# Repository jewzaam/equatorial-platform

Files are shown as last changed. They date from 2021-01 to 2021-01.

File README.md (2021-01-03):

Welcome to my equatorial platform journey.  This is a work in progress, but I'm pretty obsessed with it lately so expect to get something built to test it out soon.

License: [CC BY-NC-SA-3.0](https://creativecommons.org/licenses/by-nc-sa/3.0/)

Documents are in the [docs](docs/) directory.

OpenSCAD source is in the [src](src/) directory.

Generated STL is in the [stl](stl/) directory.

# Docs Index

* [Introduction](docs/05-introduction.md)
* [Getting Started](docs/10-getting-started.md)
* [Model: Platform Top](docs/30-model-platform-top.md)
* [Model: Platform Bottom](docs/50-model-platform-bottom.md)
* [References](docs/99-references.md)

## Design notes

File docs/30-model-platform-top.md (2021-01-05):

# Model: Top Platform

## Basic Platform
For the purposes of this document the platform (brown) is represented as a triangle.  In practice it can be whatever shape you like so long as it’s heavy enough and your telescope fits on it.
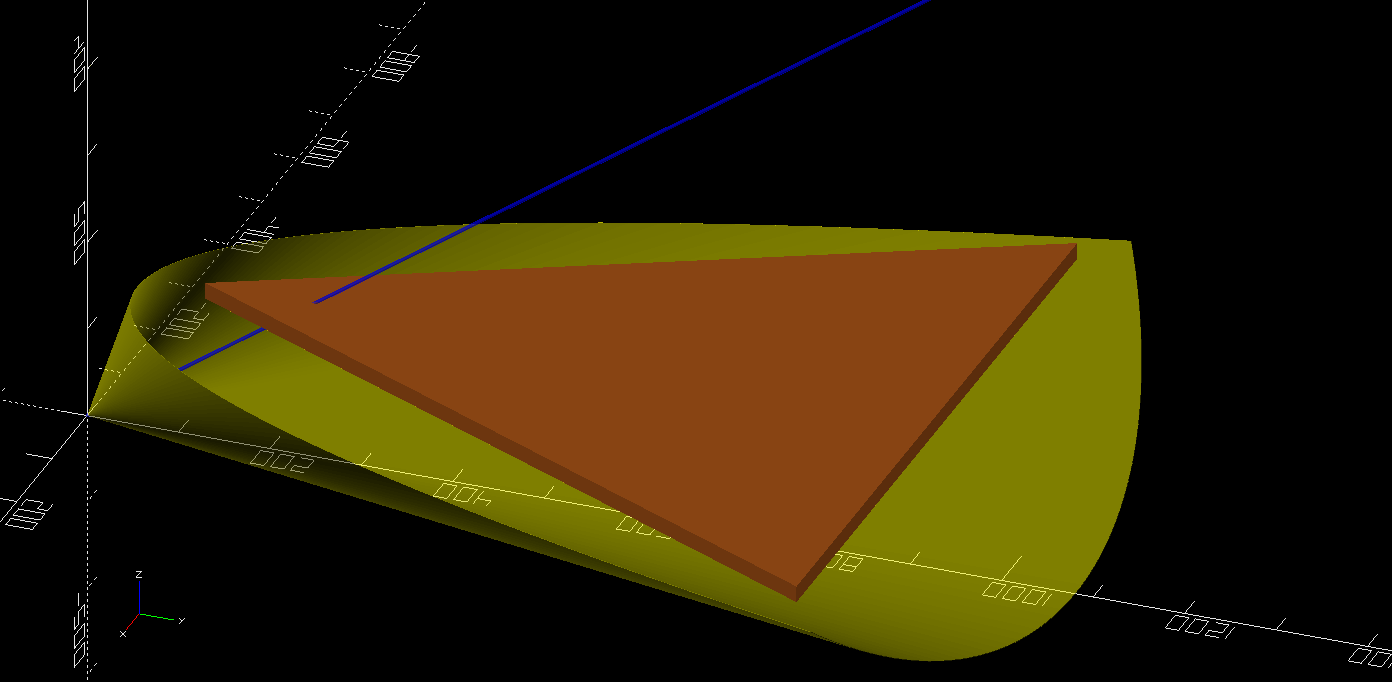
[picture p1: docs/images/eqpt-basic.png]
Basic Platform


## Our Cone
The foundation of an equatorial platform is spilling a cone (yellow) to compensate for earth’s rotation.  So we take the latitude where the platform is going to be used and start with a cone on its side with the center axis (blue) raised at the latitude.
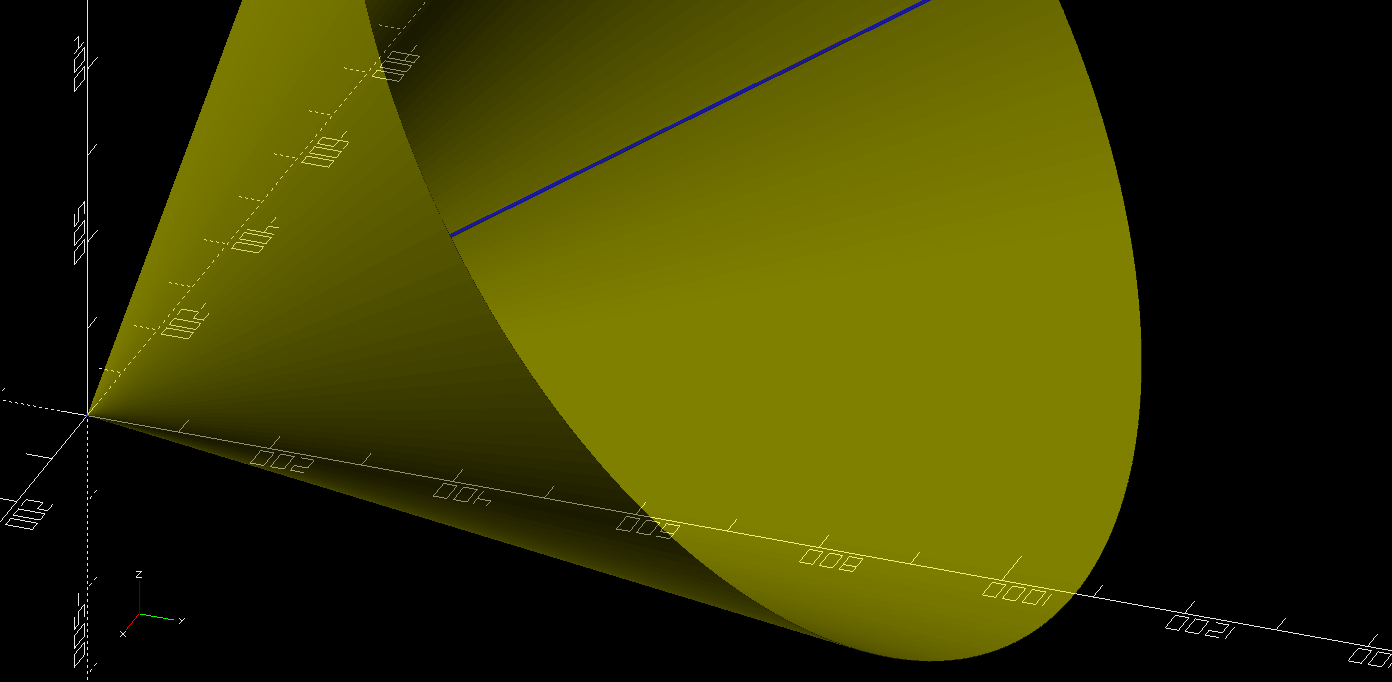
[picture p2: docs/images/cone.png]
Cone


## South Bearing
The entire model depends on this platform, south bearing pivot pin (purple), and the distance the bottom and top of the platforms are from each other at the north bridge (not built yet).

With this critical information we can find the intersection of the bottom of the platform with the cone.  This is the plane with the platform positioned off the bottom of the cone with the south bearing pivot pin touching the axis.  We illustrate this by cutting the top of the cone off showing the parabola edge.
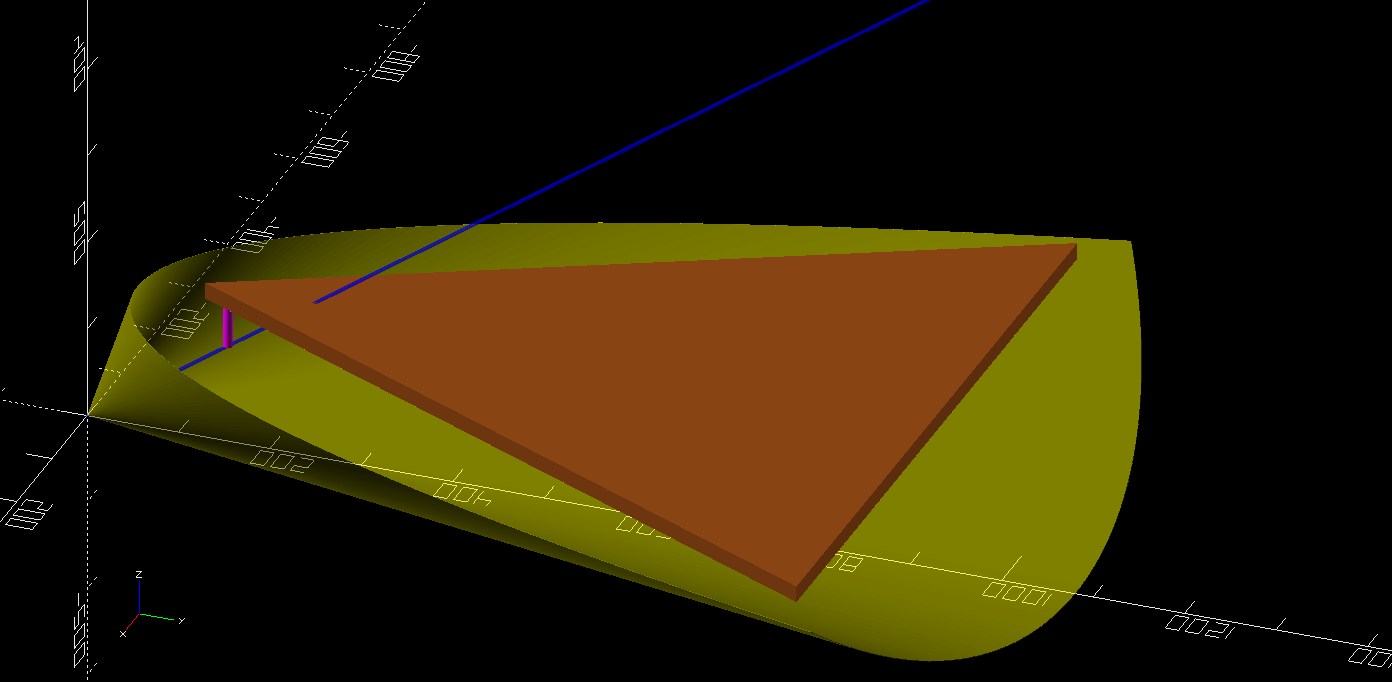
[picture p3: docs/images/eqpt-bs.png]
South Pin


## Rotation
Things get interesting now!  We want to design the north bridge. At the north bridge we have movement along a curve.  This movement means a lot of moving forces and ideally we have the forces go straight down.  This will also simplify where this curve rests (and moves) on the bottom platform.  To find this curve that intersects the cone directly under the middle of the north edge of the platform and is perpendicular to the axis.  In this picture a slice of the circle (green) is shown with the platform removed for better viewing.
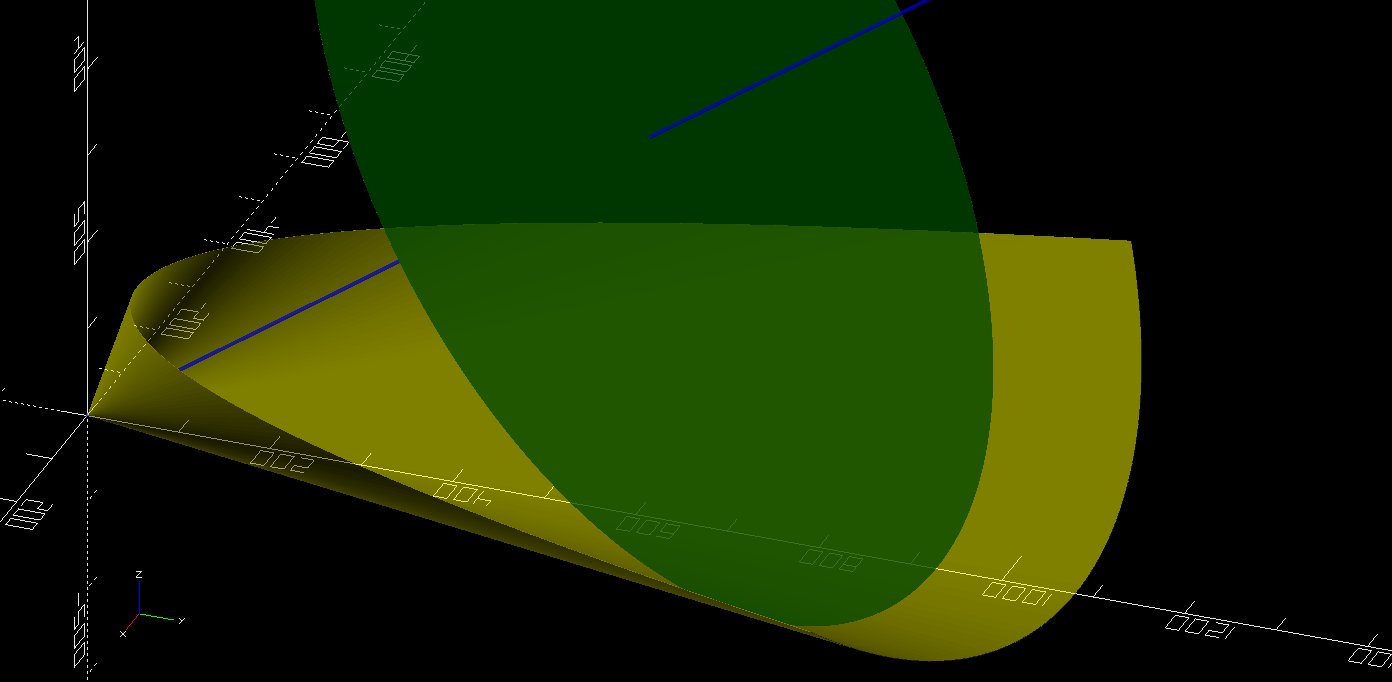
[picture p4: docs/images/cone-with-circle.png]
Cone with Circle


## Platform with Rotation
To verify, we can review the model with the platform (brown) added in, the circle (green) cut, and a rod (red) indicating the circle under the platform edge lines up.
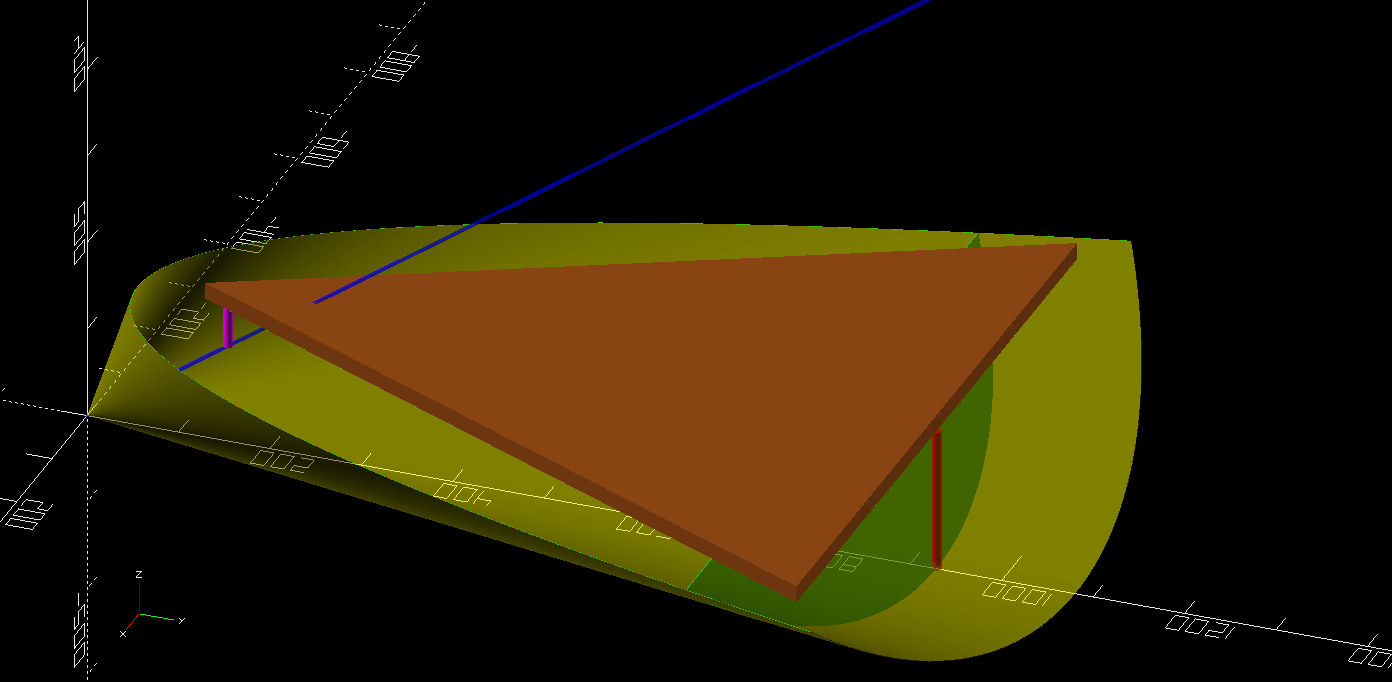
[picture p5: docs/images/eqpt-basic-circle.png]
Cone with Circle and Basic Platform


## Point on Parabola
That looks fancy and complicated.  But why do we care?  We want a vertical north bearing.  For that we are going to find where the circle in the picture above ends on the cone.  Meaning, the point (pink) on the parabola that intersects with the circle.  From that point we’ll create a curve towards where the cone (red) intersects with the circle.
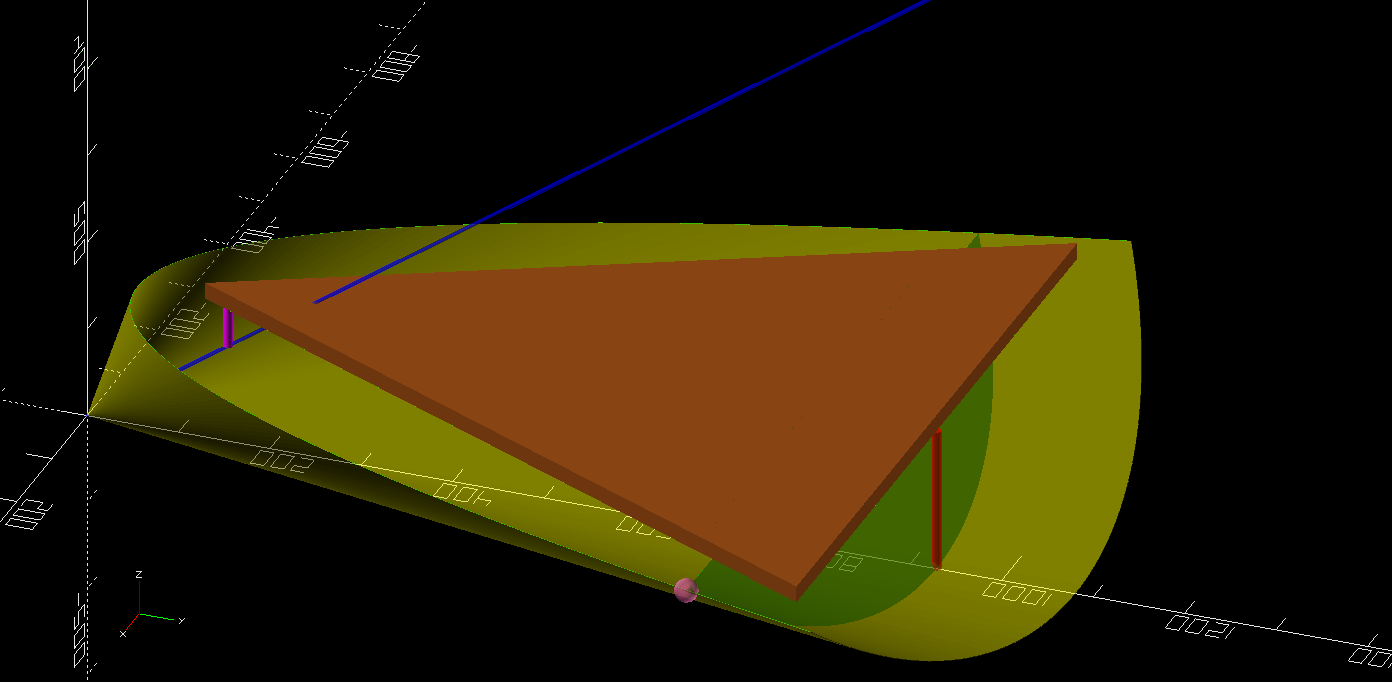
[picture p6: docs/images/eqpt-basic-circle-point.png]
Cone with Circle and Basic Platform and Point


## Adjusted Platform
Except… this isn’t what we really want.  We want the curve from where the green circle intersects the cone between platform edges.  And we have to consider we’re not making the full curve since we’ll never be able to use the middle portion.

Ok, this needs to be adjusted!  We need to line up the circle with the east and west edges of the platform.  I’m going to optimize a little bit.  I know I won’t have a triangular corner on my platform.  So I’m going to simply square the north edge corners. I’ll use the intersection of the circle on the parabola since it’s close enough to what I want and can be consistently calculated from the input we already have.
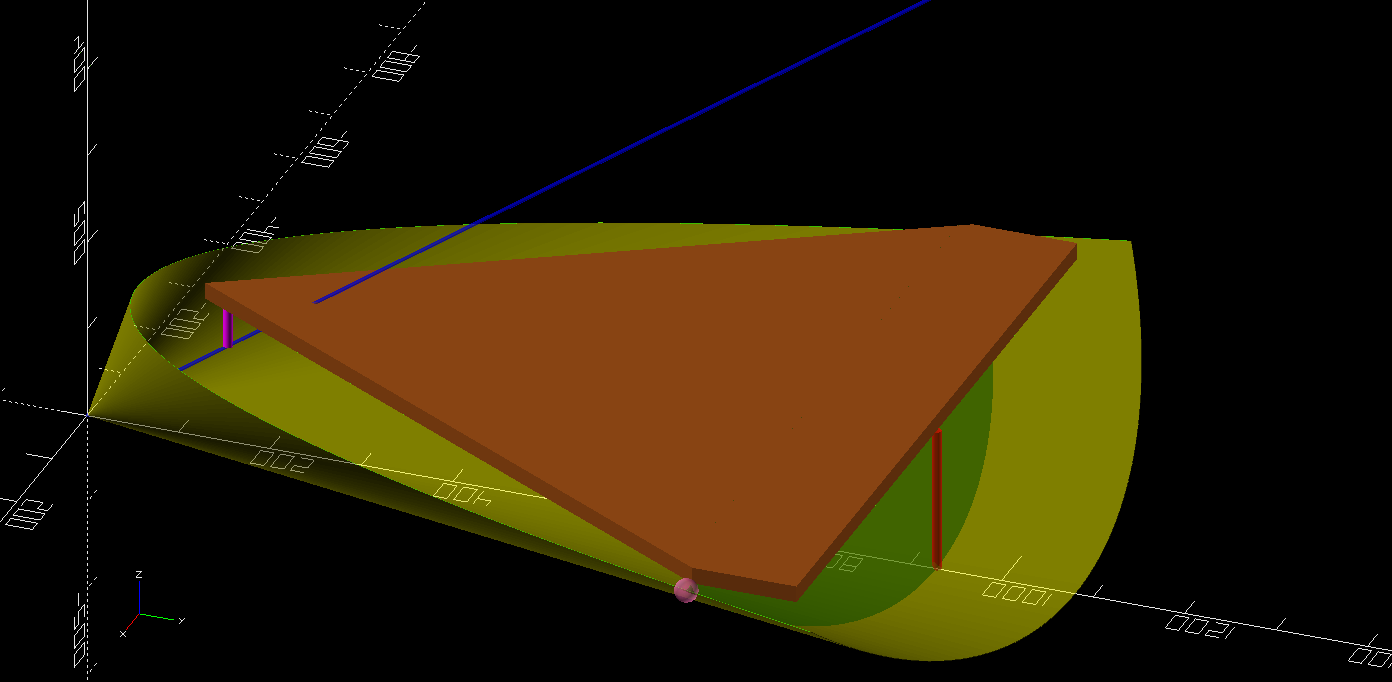
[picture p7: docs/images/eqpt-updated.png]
Updated Platform


## North Curve: Rough
Now we’ll build the north curve.  Finally!  Deep breath.. we move to “close enough” territory now.  Drop a rectangle (orange) along the edge from the circle/parabola/platform intersection (pink) towards the rod (red).  Limit the width to the print area assuming you can print the height.

Note the north rectangle (green) does not touch the full circle (green).  You would need to adjust the height of this part to get it to hit all bits of the curve.  Remember, we’re trying to have forces go straight down from the platform.  The simplest approximation of this is to base it on a flat orientation.
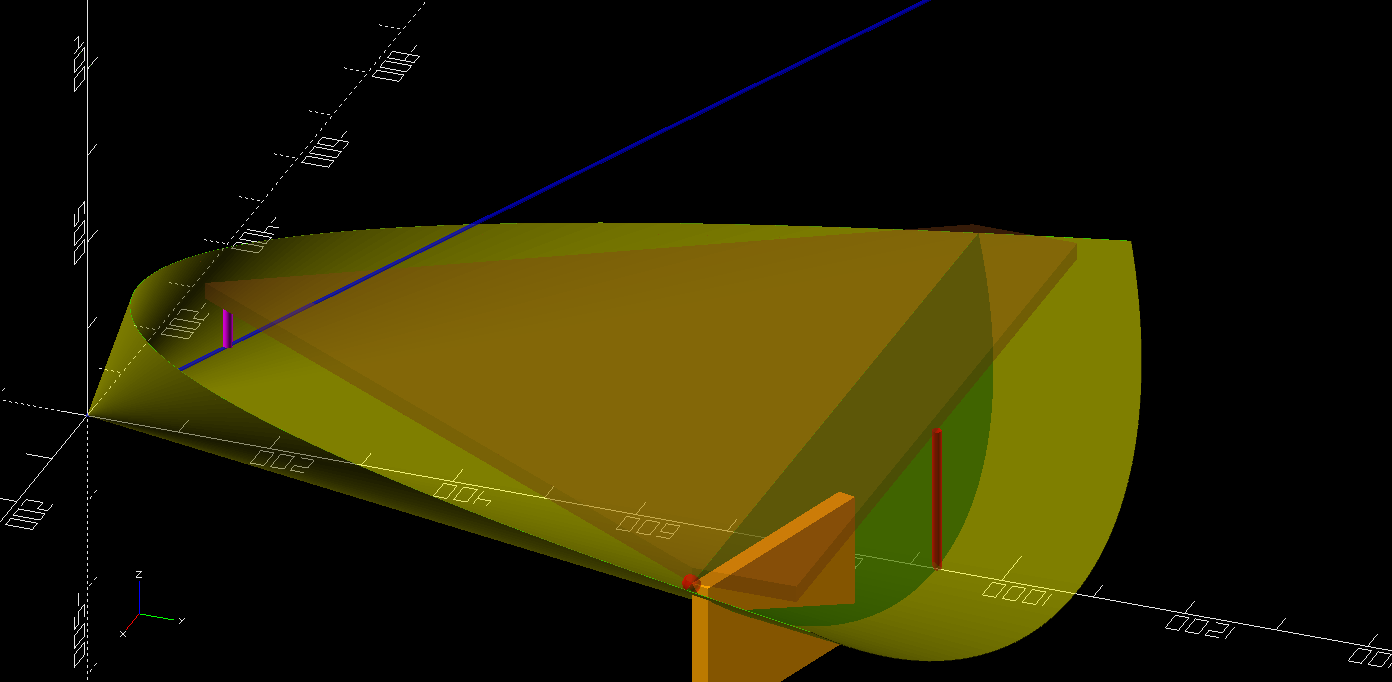
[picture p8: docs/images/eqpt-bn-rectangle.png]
North Rectangle


## North Curve: Pretty Good
There are some thing that could be optimized about this.  But keep in mind this is about rotating around the axis (blue).  And we have the cone (yellow) that provides a surface.  If we simply ensure that our north curve (orange) roles on something that represents the outside of the cone we’re good.  
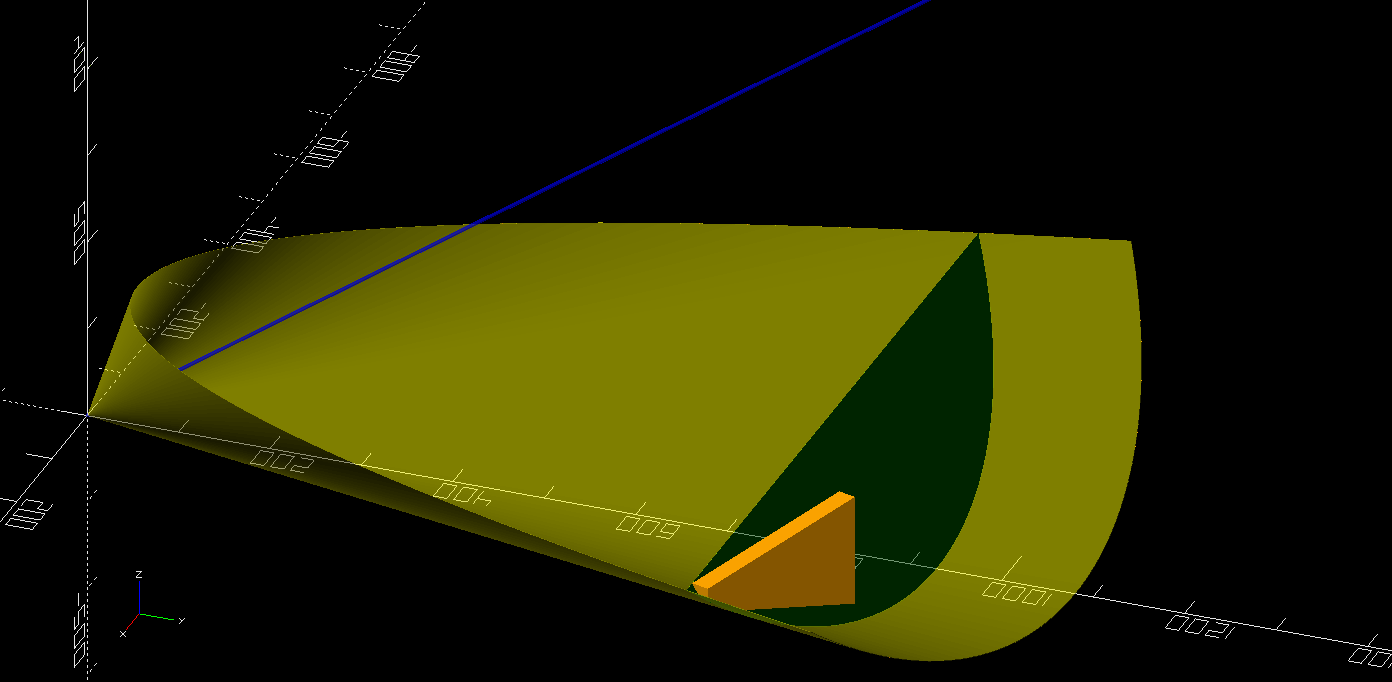
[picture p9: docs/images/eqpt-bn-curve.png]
North Curve


## North Curve: Fancy
I couldn't leave it alone though.  When looking at placement for the bearing under the north curve (orange) I just didn't like that it moved across that curve.  So we get fancy.  I'll explain it but not going to show anything but the final product (purple).

1. draw the circle with a height that's acceptable for it to run on the bearing(s)
2. cut the top off at the bottom of the platform
3. cut the inside portion of the remainder off so that a width that is big enough to print remains
4. cut all but the outer edge of this curve off
5. place a copy of this curve offset in the z direction by the platform bottom's height
6. create a shape between the two curves (original and copy) with [hull](https://en.wikibooks.org/wiki/OpenSCAD_User_Manual/Transformations#hull)
7. cut again, keeping only the portion below the platform's bottom
8. and cut one more time to curve the inner vertical to match the outer vertical
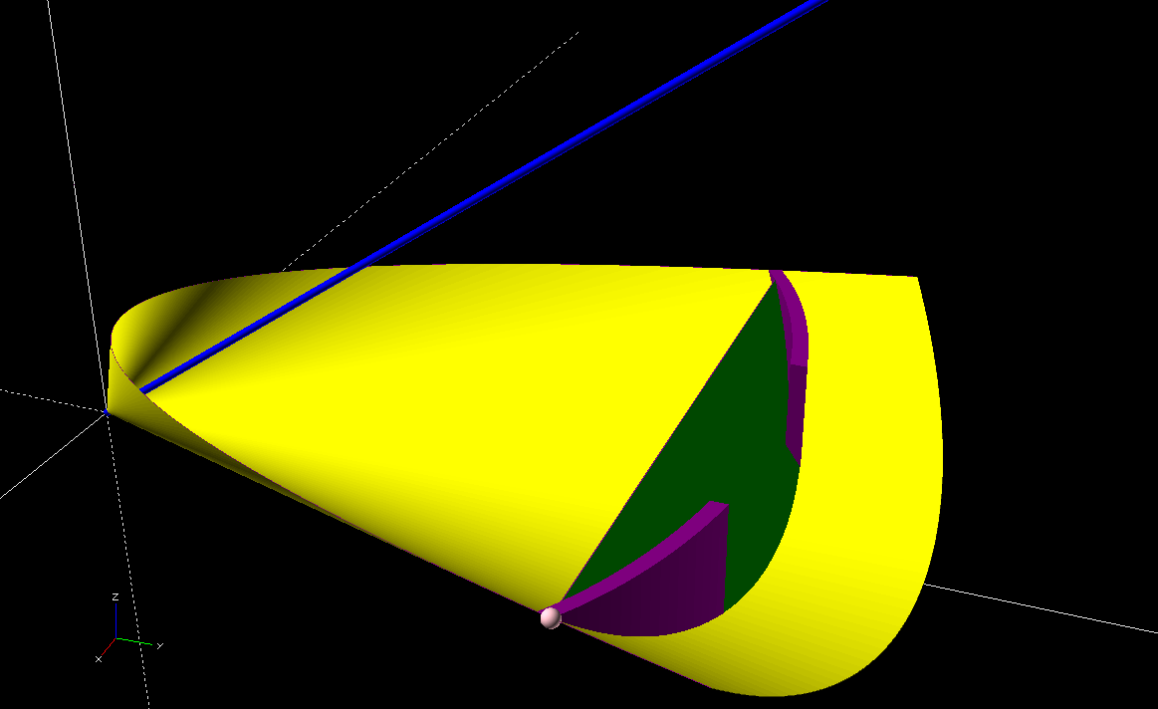
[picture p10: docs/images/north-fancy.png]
North Fancy


## North Curve: Supports
The edge of the circle now lines up with the fancy north curve.  But on the off chance it’s not good enough we can ensure the platform can take adjustments.  We’ll build the mounting support relative to the point on the parabola (pink) so adjustments will just screw in to replace the old part.  Use the washer diameter to limit the printed horizontal support structure.  It doesn’t add value if it’s not being held by something.
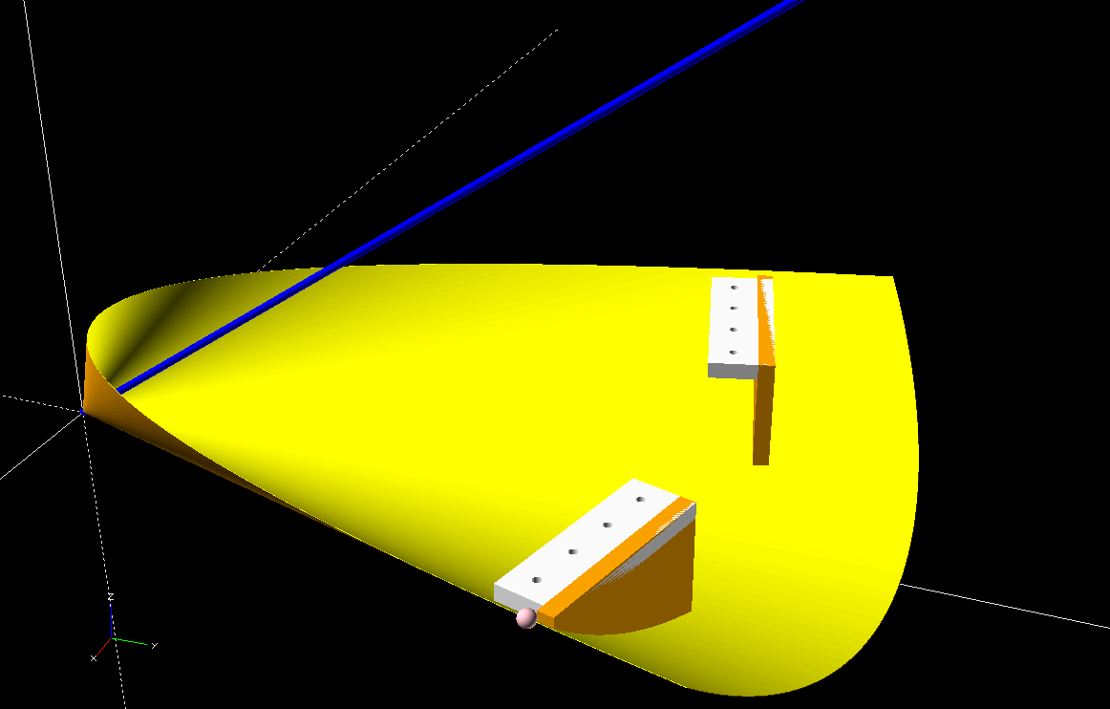
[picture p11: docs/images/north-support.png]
North Support


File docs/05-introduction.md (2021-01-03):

# My journey in building an equatorial platform

## Why?!
I want to see what I can do with the telescope my kids got for Christmas.  It’s great for seeing things but objects move so fast.  And I find I really like taking pictures.  Better pictures require more time for exposure.  More time means moving the scope to stay on target longer.

## What is an equatorial platform?
"An **equatorial platform** or equatorial table is an equatorial telescope mount in the form of a specially designed platform that allows any device sitting on it to **track astronomical objects** in the sky **on an equatorial axis**."<br>
https://en.wikipedia.org/wiki/Equatorial_platform 

You live on earth.  Earth isn’t stationary.  When we see the stars move at night it is because of the spin of the earth on its axis (blue).
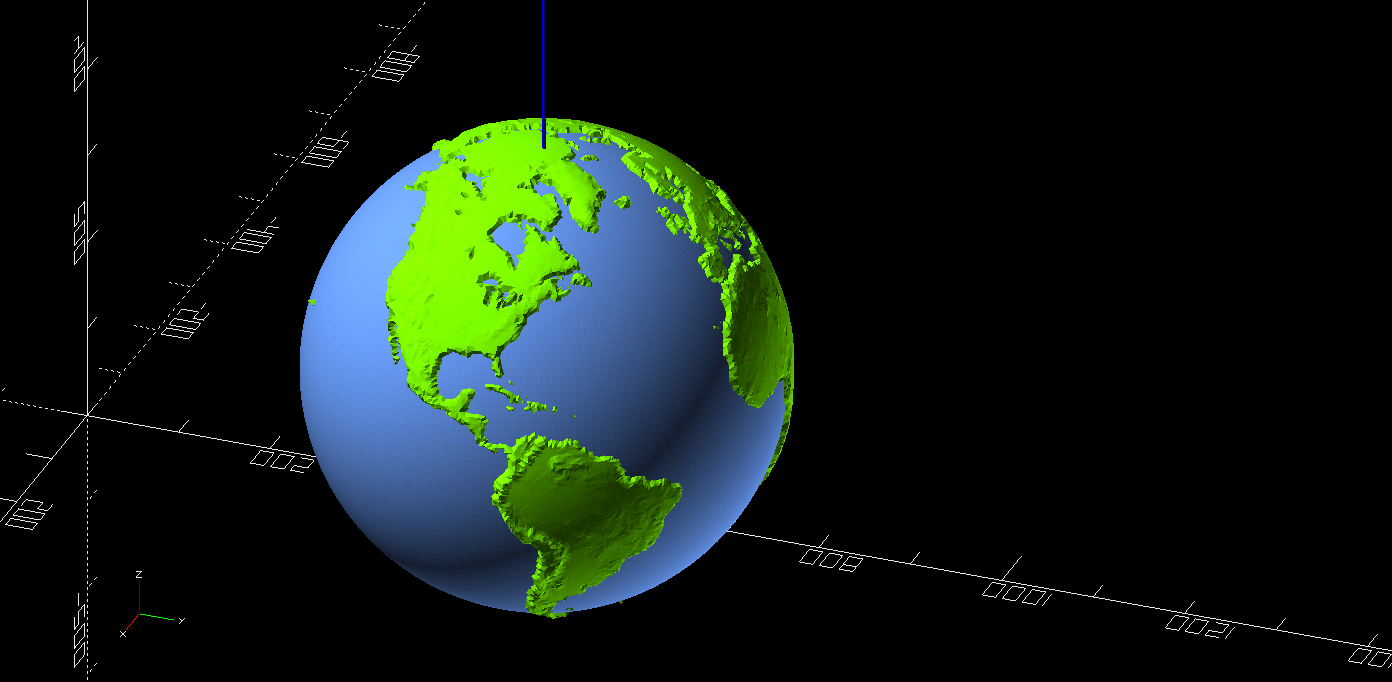
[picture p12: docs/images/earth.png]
Earth


When trying to _compensate for the movement of the earth_ when looking at celestial objects (moon, planets, stars, nebula, etc) you need something to move you in opposition of that rotation.  If you draw a line directly from where you are toward polar north (or south if in the southern hemisphere) and then draw a cone (yellow) around that such that the cone is perpendicular to the ground, you have the rotation you need.
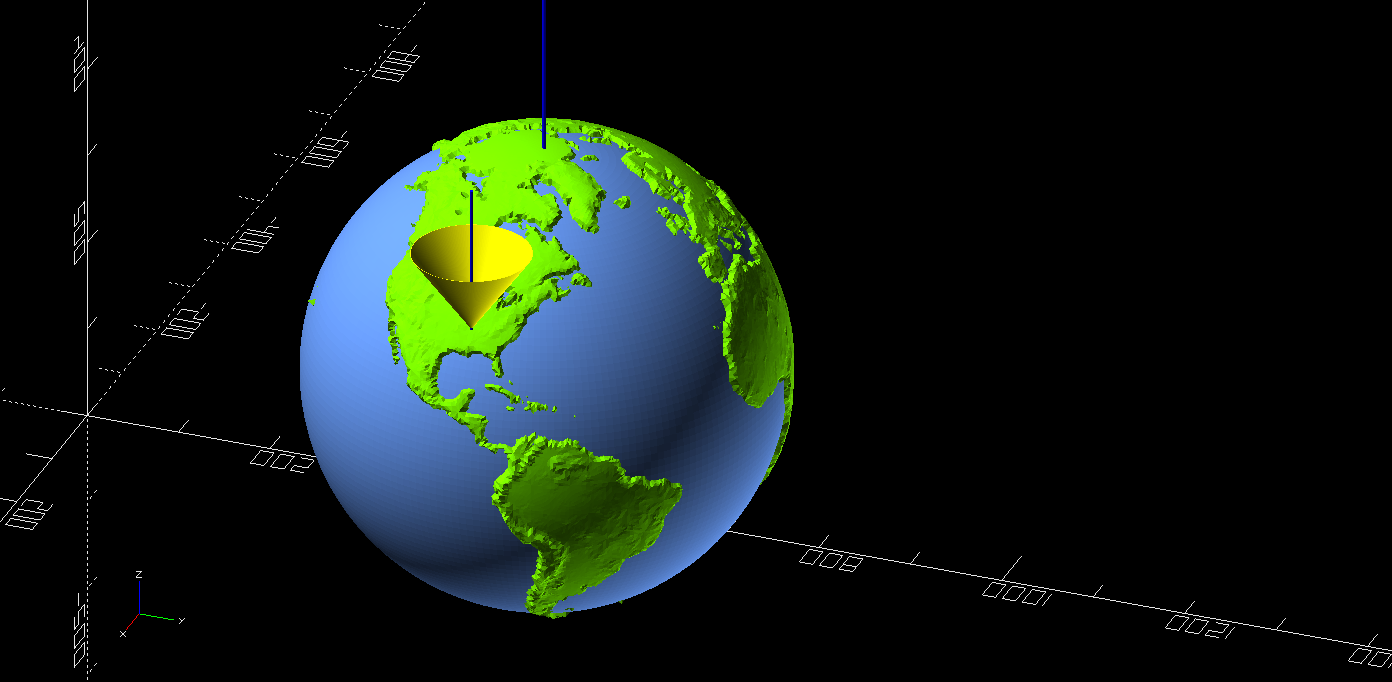
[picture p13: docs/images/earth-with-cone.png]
Earth with Cone


You need something to move your reference to negate the spin from the planet.  There are many ways to do this, one is an [equatorial platform](https://en.wikipedia.org/wiki/Equatorial_platform).

Ultimately you'll have a platform with two parts, a top and bottom.  This platform rotates around the axis.  The bottom houses bearings and one or more motors.  The top is where the telescope rests and is what is moved by the motor(s).  

TODO: picture of final platform, maybe animated gif?

# What do you need to know?
You can’t just make one unless you have some software to do the math and hardware to make the final product.  There are companies that will do that for you, but they tend to be for larger scopes than I have and cost a LOT more money than I want to spend (5x more than my scope is new).

So, learn some things and do some math and you can make the platform.  There isn’t a single post on the interwebs that had all I needed.  This section hits the high points of the things I needed to learn.

## Trigonometry
Ok, I lied.  I know this.  But if you don’t you’ll need to do some reading.  If you’re looking at building this platform yourself you very likely know this is important.  If you didn’t this is the foundation by which you calculate all the things for this platform.  You need to know it..  I reference the wikipedia’s Trigonometry page to make sure I have it right, but also remember sohcahtoa.

## Center of Gravity (CoG)
When you put your telescope on a platform that will tilt it is good to know the telescope will not fall over.  Therefore knowing the center of gravity (CoG) is critical.  After a lot of reading and musing about this I settled on a simple calculation that will approximate CoG well enough.  But what if you want to know the real CoG for the finished product?  Ok, you can do that..

### CoG: The Hard Way
Take the top of the equatorial platform and secure it to the bottom of your telescope rocker box in the position it would be when being used.  Make sure NOTHING will come loose cause it’s going to get interesting…  Find an eyebolt in a ceiling or some other stable structure you can hang the whole assembly on.  Tie a line strong enough to carry the weight of the scope plus platform.  Pick a point on the bottom of the platform and suspend the whole assembly upside down from the ceiling.  Note the line straight down from that point through the suspended apparatus.  Take it all down, pick another point, and do it again.  The CoG is where the two points intersect.

Not having done this method I would setup a camera to take a picture of each one of these sessions and then hack around in some image software, probably GIMP, to find where things intersect.  If nothing else, eyeball it to get a rough CoG height.  Note this method will get you the distance from the bottom of the equatorial platform board.  The “Easy Way” method uses the bottom of the cone which is NOT THE SAME THING.  You can fix this by adding some known height to the value you calculated / eyeballed and call it a day.

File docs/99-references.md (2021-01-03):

# References

* [Equatorial platform](https://en.wikipedia.org/wiki/Equatorial_platform)
* [Trigonometry](https://en.wikipedia.org/wiki/Trigonometry)
* [Sohcahtoa: Sine, Cosine, Tangent](https://www.mathsisfun.com/algebra/sohcahtoa.html)
* [Conic section](https://en.wikipedia.org/wiki/Conic_section)
* [center of gravity | Definition & Facts](https://www.britannica.com/science/centre-of-gravity)
* [5 Ways to Calculate Center of Gravity](https://www.wikihow.com/Calculate-Center-of-Gravity)
* [Imaging planets with a Dobsonian telescope - skyatnightmagazine](https://www.skyatnightmagazine.com/astrophotography/astrophoto-tips/imaging-planets-dobsonian-telescope/)
* [Telescopes and Deep Sky by Reiner Vogel](http://www.reinervogel.net/index_e.html?/Plattform/plattform_VNS_e.html)
* [Making an equatorial platform - ATM, Optics and DIY Forum](https://www.cloudynights.com/topic/35576-making-an-equatorial-platform/)
* [How can find CG of dobsonian telescope? - ATM, Optics and DIY Forum](https://www.cloudynights.com/topic/359479-how-can-find-cg-of-dobsonian-telescope/)
* [3D printed Equatorial platform - Mounts](https://www.cloudynights.com/topic/696090-3d-printed-equatorial-platform/)

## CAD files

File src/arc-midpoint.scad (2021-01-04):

/*

Now that I know how to get the coordinates of a point on a circle given the angle and radius (see circle.scad) we need to find the midpoint for an arc.

We know:
- radius (hard coded to 100 in this example)
- coordinates of the two points A and B

And we can assume all is within one quadrent.  A is up and to the left of B.
*/

A_x=90.6308;
A_y=42.2618;

B_x=57.3576;
B_y=81.9152;

/* [Hidden] */

$fn=100;
$vpt=[0,0,0];
$vpr=[360,0,0];
$vpd=800;

r=100;

module point(x,y,c) {
    color(c)
    translate([x,y,0])
    sphere(d=10);
}

module rod(angle,c) {
    color(c)
    rotate([0,0,-angle])
    {
        rotate([-90,0,0])
        cylinder(r=2,h=r,center=false);

        // and, cause we can, label it
        translate([-len(str(angle))*10/3,r+5,0])
        text(str(angle,"°"));
    }
}

module reference_circle() {
    color("gold")
    cylinder(r=r,h=1,center=true);
}

function midpoint(r,x1,y1,x2,y2) = [r*sin(atan(x1/y1)+(atan(x2/y2)-atan(x1/y1))/2),r*cos(atan(x1/y1)+(atan(x2/y2)-atan(x1/y1))/2)];


// circle
reference_circle();

// the 0 degree line
rod(0,"white");

point(A_x,A_y,"Magenta");
point(B_x,B_y,"Lime");

// calculate the angles
A_T=atan(A_x/A_y);
B_T=atan(B_x/B_y);

// verify visually
rod(A_T,"Magenta");
rod(B_T,"Lime");

// we know the angles now, draw midpoint line
M_T=A_T+(B_T-A_T)/2;
rod(M_T,"Silver");

// calculate the midpoint coordinates
// https://math.stackexchange.com/questions/260096/find-the-coordinates-of-a-point-on-a-circle
M_x=r*sin(M_T);
M_y=r*cos(M_T);
point(M_x,M_y,"Silver");

// try the midpoint formula
Mxy=midpoint(r,A_x,A_y,B_x,B_y);
point(Mxy[0],Mxy[1],"Gold");


// it works if the silver line has a gold point (it should overlap the silver point)

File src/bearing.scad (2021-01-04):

/*

Model of the bearing centered at (0,0,0), oriented along the x/y plane.


https://spinnermint.com/img/guides/bearing-exploded-view-265.jpg

Parts:
- inner race
- outer race
- shield

Quatlifiers:
- od: outer diameter
- id: inner diameter
- h: height

All units are in millimeters.

*/

/* [Debug] */

// If true will render the bearing.  Default to false for easy import to other models.
display=false;


/* [Hidden] */

module bearing_part(od,id,h) {
    translate([0,0,-h/2])
    difference()
    {
        cylinder(d=od,h=h);
        
        translate([0,0,-h/2])
        cylinder(d=id,h=h*2);
    }
}

module bearing(i_od,i_id,i_h,o_od,o_id,o_h,s_h) {
    union()
    {
        // outer race
        color("Silver")
        bearing_part(od=o_od,id=o_id,h=o_h);

        // inner race
        color("Silver")
        bearing_part(od=i_od,id=i_id,h=i_h);

        // shield
        color("SlateGray")
        bearing_part(od=o_id,id=i_od,h=s_h);
    }
}

// for debugging
if (display) {
    $fn=200;

    race_inner_od=21;
    race_inner_id=14.9;
    race_inner_h=11;

    race_outer_od=35;
    race_outer_id=30.8;
    race_outer_h=11;

    shield_h=10.4;

    bearing(
        i_od=race_inner_od,
        i_id=race_inner_id,
        i_h=race_inner_h,
        o_od=race_outer_od,
        o_id=race_outer_id,
        o_h=race_outer_h,
        s_h=shield_h
    );
}

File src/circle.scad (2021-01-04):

/*

Needed to find the mid-point of an arc on a circle.
This is a building block towards that:

Find the coordinates of a point on a circle given an angle.

*/

angle=145;

/* [Hidden] */

$fn=100;
$vpt=[54,0,0];
$vpr=[360,0,0];
$vpd=800;

r=100;

color("gold")
cylinder(r=r,h=1,center=true);

// column represetning 0 degress
color("pink")
rotate([-90,0,0])
cylinder(r=2,h=r,center=false);

translate([-10/2,r+5,0])
text(str("0°"));

// put a point 45 degrees off the y axis
P_T=angle;
P_x=r*sin(P_T);
P_y=r*cos(P_T);

color("lime")
translate([P_x,P_y,0])
sphere(r=5);

// verify with a rotated cylinder

color("blue")
rotate([0,0,-P_T])
{
    rotate([-90,0,0])
    cylinder(r=2,h=r,center=false);

    // and, cause we can, label it
    translate([-len(str(P_T))*10/3,r+5,0])
    text(str(P_T,"°"));
}


translate([0,0,100])
text(str(P_x));

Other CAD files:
src/equatorial-platform-docs.scad
src/model-dobsonian.scad

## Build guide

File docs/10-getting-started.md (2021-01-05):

# Getting Started!

## Principles Defined
I’ve done many iterations on this and they’re all flawed.  The assume a dynamic platform.  This is a problem because it makes the build unable to adjust for error.  If your math is wrong you have to build a new platform.  I have decided a set of principles upon which the design is based is necessary.

1. The platform must have known dimensions.
2. The user defines the final configuration for both north and south bearings.
3. The design checks the telescope fits on the platform.
4. The design checks the center of gravity but not use it in the design.

This gives us a solid foundation to build from.  We can validate the design by doing a check that the platform and telescope should not tip over ever.  And we give the user ultimate responsibility for getting things right.

## Principles in Action
This actually is just the user inputs.  For this parameterized build, we can only work on what the user tells us.  So we need to collect some key information.  Listing those here in the context of the principles defined earlier:

1. The platform must have known dimensions.
    * platform top max width (east / west)
    * platform top length (north / south)
2. The user defines the final configuration for both north and south bearings.
    * south bearing pivot pin length
    * south bearing pivot pin diameter
    * center of south bearing pivot pin distance from south side of platform
    * north bearing width (if 3D printing, probably your max print bed width)
    * north bearing height at center (aka distance from bottom board to top board)
3. The design checks the telescope fits on the platform.
    * rocker box radius
4. The design checks the center of gravity but not use it in the design.
    * rocker box weight
    * tube weight
    * rocker box weight
    * rocker box distribution factor (i.e. how bottom heavy is it)
    * platform top weight
    * platform top thickness

From #1 we can provide a template for the platform top.  This template is used by the builder to at a minimum estimate the platform weight.

From #2 in conjunction with #1 we know the height of the south bearing and the curvature of the north bearing.  With data from #4 we can calculate if the scope will ever fall over, meaning tip past the point that gravity can keep things from moving in an unstable way.

And #3 will ensure what is being built actually fits the telescope.  Seems obvious but let’s make sure!

## Designing the Model
I use OpenSCAD.  All the images taken are from this tool.  The [model used is included](../src/equatorial-platform-docs.scad) and each picture can be reviewed by picking the “image” parameter.  The constant input values are also available for editing.

There are some lessons I have learned doing this project that I want to share.  As I figure out better ways to do the models I have started over or made major revisions.  Starting over is easier for me but that's up to the individual.  I'm on revision 6 as of writing these tips..

1. pick a point of reference for all shapes
1. do translations from this point of reference
1. do rotations from this point of reference
1. use a standard naming convention for your variables
1. use modules to create intermediate or final shapes
1. use consistent module arguments
1. do your model in steps you can reference later (you want to know what you did before you tweaked it, i.e. why I have a "fancy" north curve)
1. for each of the steps, use a parameter to select what to render
1. use a prefix for user supplied variables that you will never use for hidden variables

For this model:
* [0,0,0] is `ORIGIN`, the point of reference for all things
* I decided to put my build along the Y axis.. probably X is more common (better?) choice but that is where I am
* I build standard variables OUTSIDE of modules and pass them in as default arguments.

Using default agruments allows for manipulation by passing new arguments without having to write a new module or manipulate the output of a module.  It's **so** much cleaner!

I have put all of my standards into the model file used for this and since it might change I don't want to recreate it here.  See [the docs model initial comments](../src/equatorial-platform-docs.scad#L3-L43) (note this may not be exactly right as I am still tweaking the model).

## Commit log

2021-01-03 Initial docs
    for intro, design foundation, and top platform
    [equatorial-platform-docs.scad, model-dobsonian.scad]
2021-01-04 Updated to blog stuff
    Fiddling with the support structure on north bridge
    [arc-midpoint.scad, bearing.scad, circle.scad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]
2021-01-05 Much of it reworked with better coordinate system
    Standardizing variables and using origin (0,0,0) as point of reference for anything material. Only exception is the "circle" at this time.
    [equatorial-platform-docs.scad]
2021-01-05 Mostly done updating eqpt and docs
    [equatorial-platform-docs.scad]
